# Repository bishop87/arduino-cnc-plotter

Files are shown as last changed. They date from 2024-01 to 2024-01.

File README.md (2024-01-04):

# CNC Plotter con Arduino

Progetto per realizzare un mini plotter cnc pilotato con arduino e motori passo passo 28byj-48

## Hardware

- 3 x motori passo passo 28byj-48 (io ho usato quelli a 5V)
- 3 x driver motori ULN2003 (solitamente venduti con i motori)
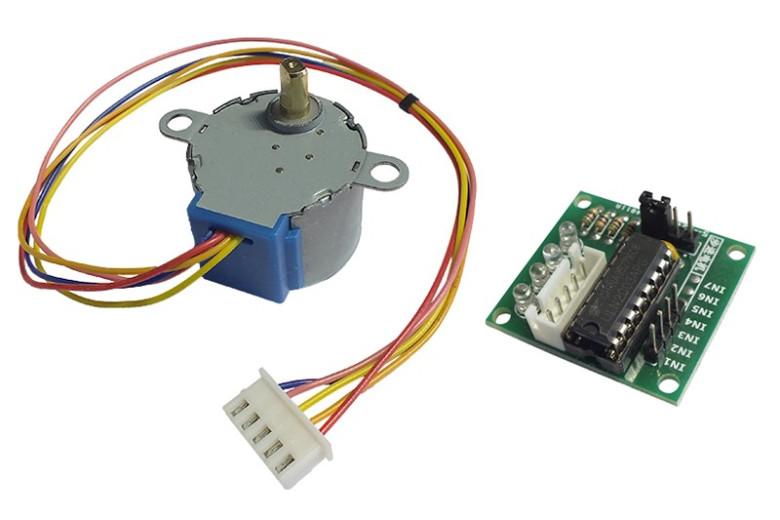
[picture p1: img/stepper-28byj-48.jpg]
stepper-28byj-48


- 1 x arduino nano
- 1 x cuscinetto a sfera tipo 608
- 1 x LM7805 (o modulo stepdown per ottenere 5V)
- 1 x alimentatore 12V
- Superficie di legno su cui fissare il materiale
- Viti varie di recupero
- Assi e supporti stampati in 3D, vedi sezione dedicata
- Pazienza, ne serve abbastanza

## Componenti 3D

Progetto Thingiverse principale da cui sono partito: https://www.thingiverse.com/thing:4796222 
Ho clonato i file stl per comodità e li ho messi nella cartella stl di questo repo:
- _SpurGear.stl_: ingranaggio da montare sul motore stepper (ne servono 2)
- _bearing_center.stl_: cilindro che restringe il foro del cuscinetto a sfera di tipo 608 per usarlo con una vite da 2-3mm di diametro
- _pen_cap.stl_: cappello da mettere sulla penna con un paio di elastici per rendere morbido l'appoggio della penna sul foglio
- _pen_holder.stl_: supporto che gestisce la penna e si fissa sul motore per l'asse Z, la parte centrale deve risultare mobile e alloggia una vite per bloccare la penna in posizione
- _plate_01.stl_: binario per l'asse Y
- _plate_02.stl_: asse Y con barra dentata
- _plate_03.stl_: binario per l'asse X
- _plate_04.stl_: asse X con barra dentata
- _prop.stl_: supporto da incollare al binario per l'asse X
- _prop_bearing_608.stl_: alternativa da usare al prop.stl se si ha un cuscinetto di tipo 608

## Assemblaggio

Video del progetto originale che illustra i vari passaggi principali sia di assemblaggio che della messa in funzione: https://www.youtube.com/watch?v=WtUIBxfddjw
Schema di collegamento dei 3 motori driver:
| Axis | Arduino |ULN2003|ULN2003|28BYJ-48|
|:---:|:---:|:-----:|:-----:|:---:|
| X-Axis | D5 |IN1 |OUT1 |BLUE |
| | D4 |IN2 |OUT2 |PINK |
| | D3 |IN3 |OUT3 |YELLOW  |
| | D2 |IN4 |OUT4 |ORANGE  |
| Y-Axis | A0 |IN1 |OUT1 |BLUE |
| | A1 |IN2 |OUT2 |PINK |
| | A2 |IN3 |OUT3 |YELLOW  |
| | A3 |IN4 |OUT4 |ORANGE  |
| Z-Axis | D13 |IN1 |OUT1 |BLUE |
| | D12 |IN2 |OUT2 |PINK |
| | D9 |IN3 |OUT3 |YELLOW  |
| | D8 |IN4 |OUT4 |ORANGE  |
| | | |+5V |RED |

## Software

 - **grbl Firmware per Arduino**: https://github.com/TGit-Tech/GRBL-28byj-48
Codice derivato dallo standard de facto per l'ambito cnc con Arduino **grbl**, consente di pilotare i 3 assi con i motori 28byj-48 ed i relativi driver più semplici dei normali stepper per cnc o stampanti 3d.
Copiare la cartella "grbl" che trovate per comodità anche in questo repo sotto il path ./lib-grbl nel path locale del PC con le librerie di ArduinoIDE (nel caso di macos /Users/nomeutente/Documents/Arduino/libraries/grbl).
 - **inkscape**: https://inkscape.org/
Famoso software open per manipolare e creare file vettoriali.
 - **jscut**: https://jscut.org/jscut.html
Consente di convertire file vettoriali svg contenenti path (eventuali font vanno convertiti in path prima con inkscape) in file gcode rispetto ai parametri della cnc configurati.
Nel path di questo repo (/jscut-settings/settings_20240105.jscut) c'è un esempio di impostazioni da caricare su jscut, nel caso è possible variare manualmente i settaggi, il pannello più importante si trova in masso a sinistra:
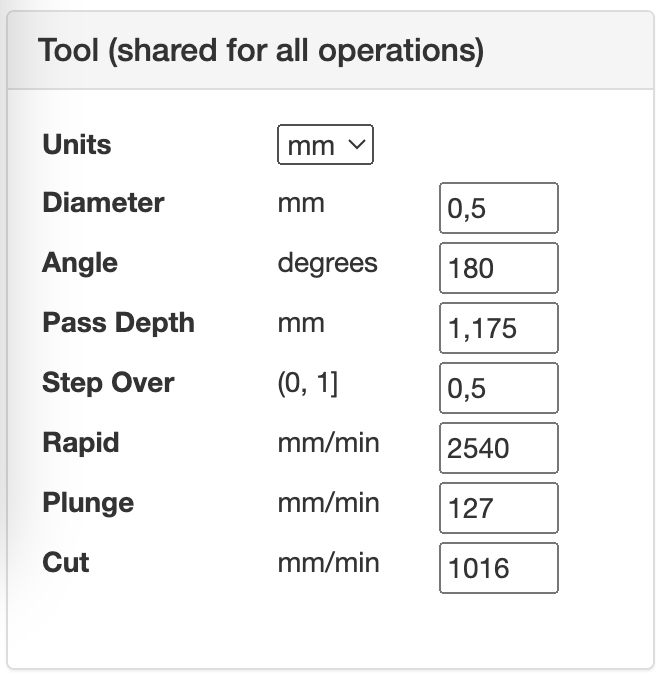
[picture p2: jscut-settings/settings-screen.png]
jscut-settings-screen


**Diameter** : sarebbe il diametro della fresa, nel nostro caso la larghezza del tratto disegnato dalla penna (più è fine più passate serviranno per disegnare)
**Pass Depth**: quanto dovrà andare in profondità la penna sull'asse z, si imposta un po' per tentativi
**Step Over**: percentuale di sovrapposizione delle varie passate, più il valore è basso più passate sovrapposte ci saranno, aumenterà di conseguenza il tempo e l'inchiostro usato.

- **UGS (Universal Gcode Sender)**: https://winder.github.io/ugs_website/
applicativo java based che consente di pilotare la cnc (il nostro arduino con firmware grbl) da PC via seriale (usb).
1. una volta aperto il programma selezionare la voce di menu "Machine" > "Setup Wizard"
2. Impostare i parametri di connessione alla porta seriale (firmware: GRBL; Port: nome della seriale a cui è collegato Arduino; baudrate: 115200), quindi cliccare "Connect"
3. Verificare la direzione degli assi X, Y, Z, ed eventualmente invertirla (io per la verità ho preferito invertire il connettore del driver su arduino per la X e la Y)
4. testare il movimento degli assi, misurando il reale spostamento rispetto al valore atteso ed inserire i parametri di step/mm calcolati dal programma (nel mio caso 72 step/mm sia per x che per y).
5. concludere il wizard senza modificare altro.

## Conclusioni

Alcune foto del risultato finale

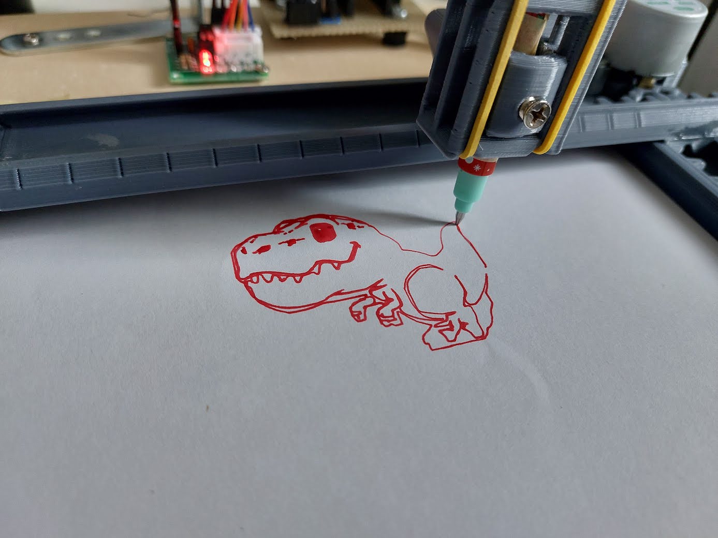
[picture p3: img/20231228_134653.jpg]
foto1


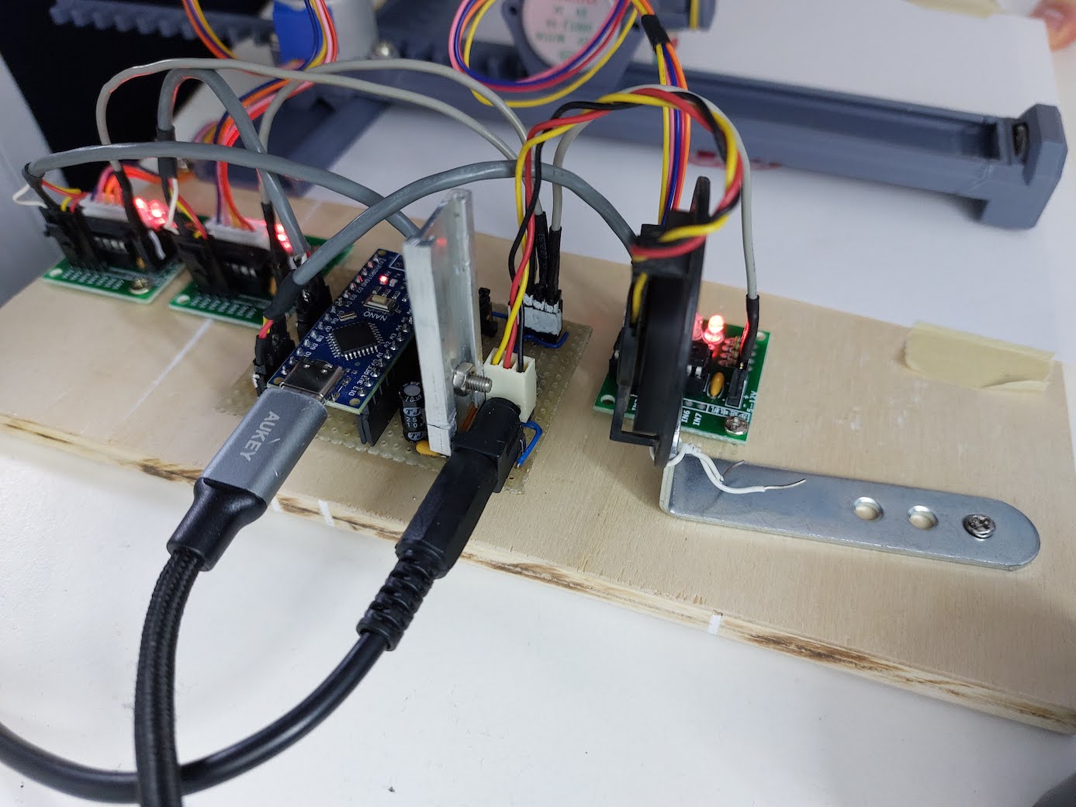
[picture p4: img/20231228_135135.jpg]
foto2


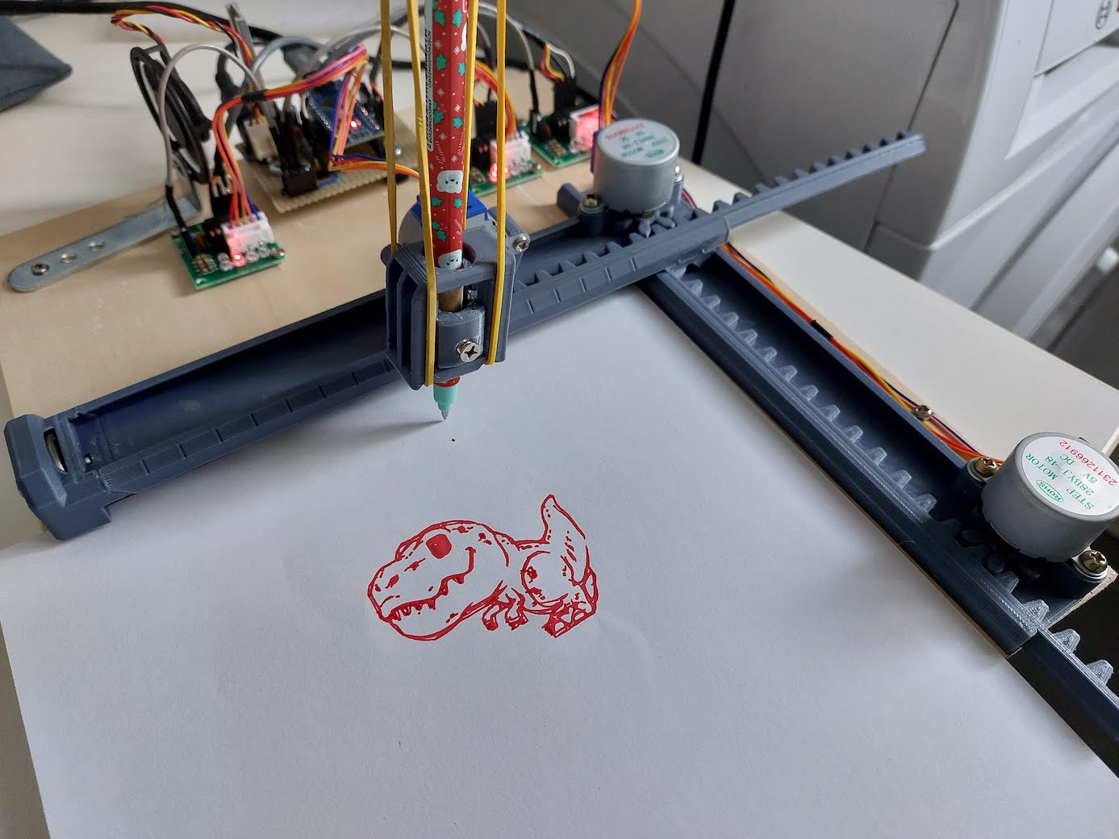
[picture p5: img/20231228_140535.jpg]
foto3


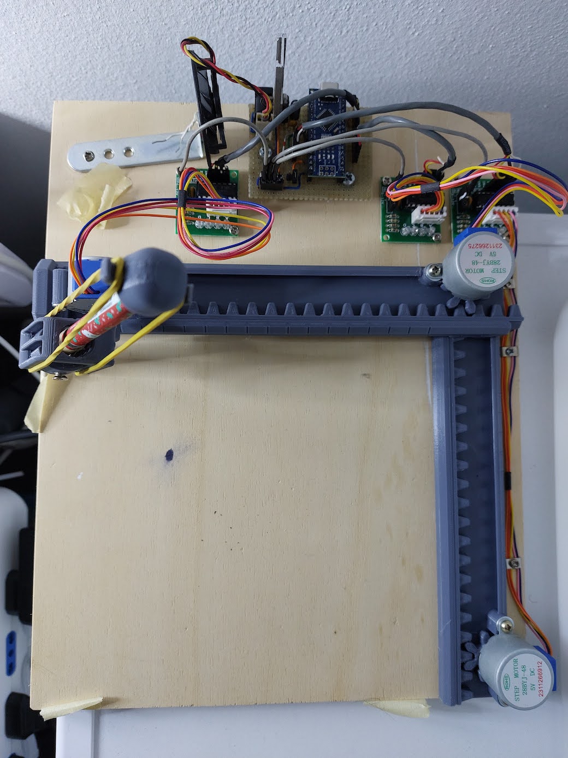
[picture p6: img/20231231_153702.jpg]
foto14


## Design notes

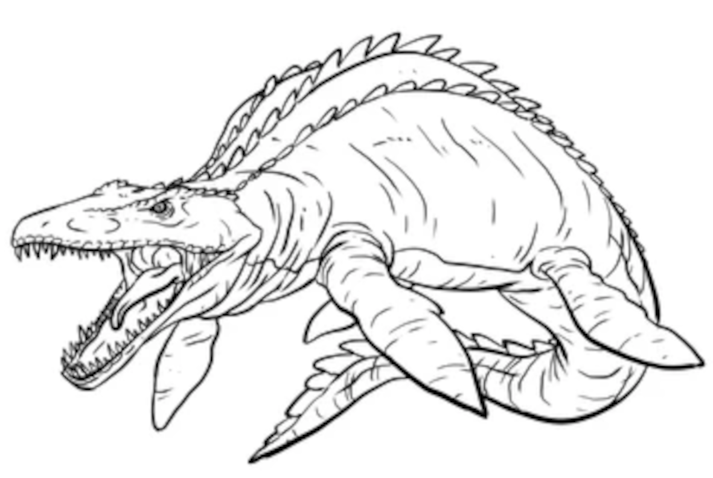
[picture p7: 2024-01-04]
example/mosa.png

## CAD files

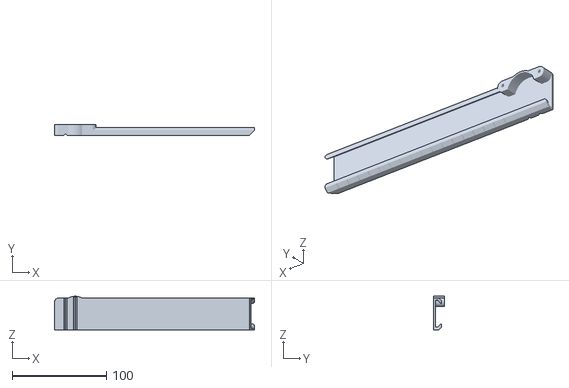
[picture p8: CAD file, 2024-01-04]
stl/plate_03.stl
211.7 x 11.5 x 35.6

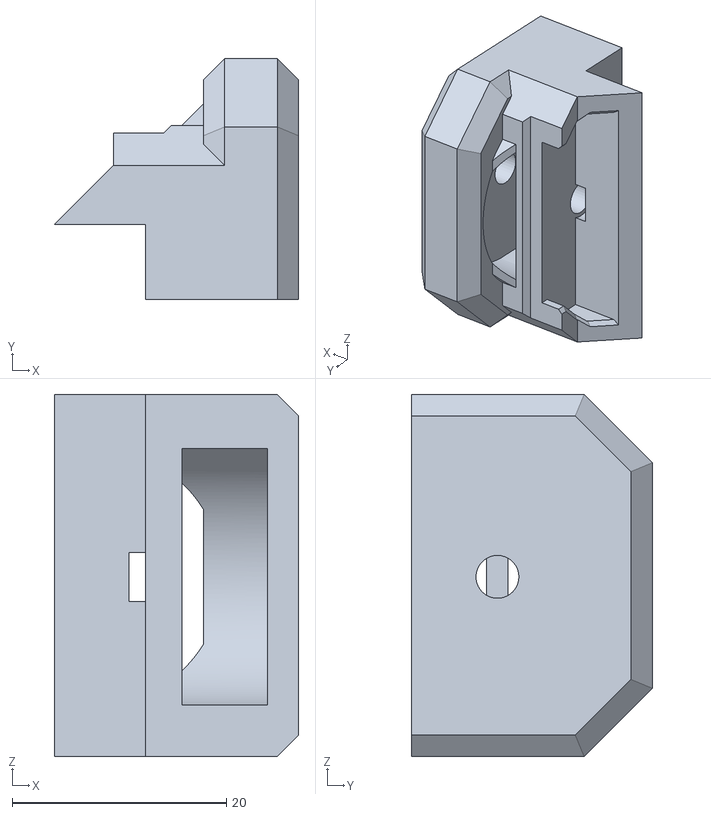
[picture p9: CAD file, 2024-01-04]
stl/prop_bearing_608.stl
22.8 x 22.4 x 33.8

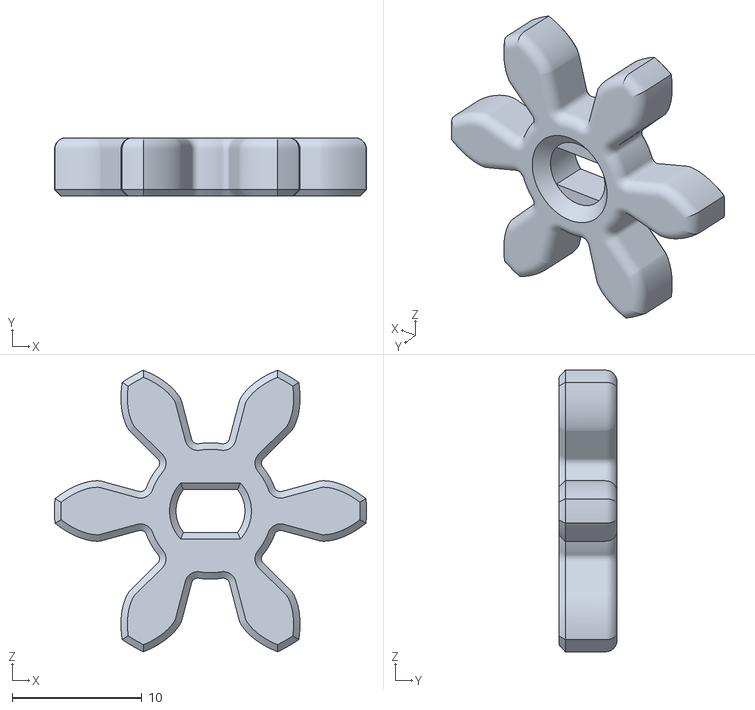
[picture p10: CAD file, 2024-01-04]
stl/SpurGear.stl
24.0 x 4.50 x 21.7

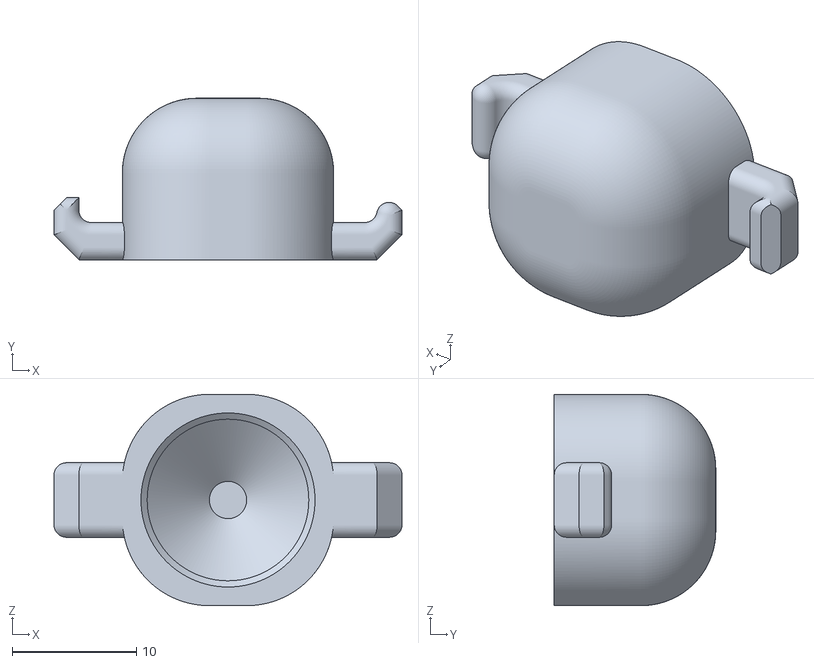
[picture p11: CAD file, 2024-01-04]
stl/pen_cap.stl
28.0 x 13.0 x 17.0

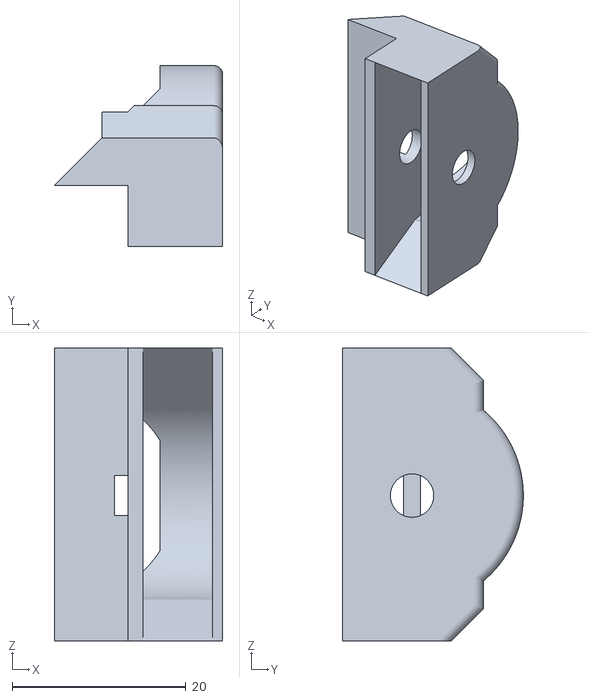
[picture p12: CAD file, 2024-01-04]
stl/prop.stl
19.4 x 20.8 x 33.8

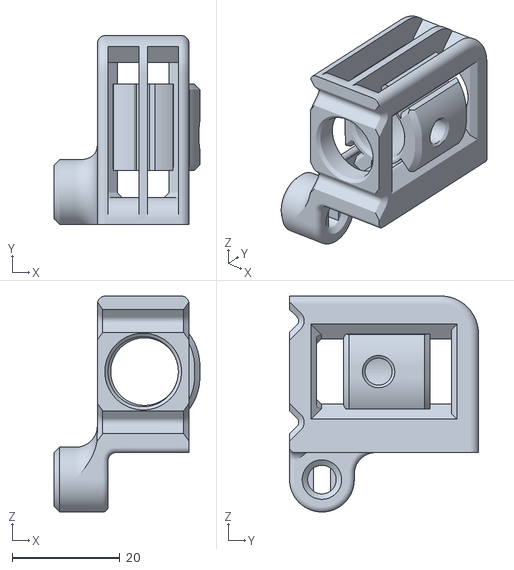
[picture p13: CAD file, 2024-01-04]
stl/pen_holder.stl
27.0 x 35.0 x 40.0

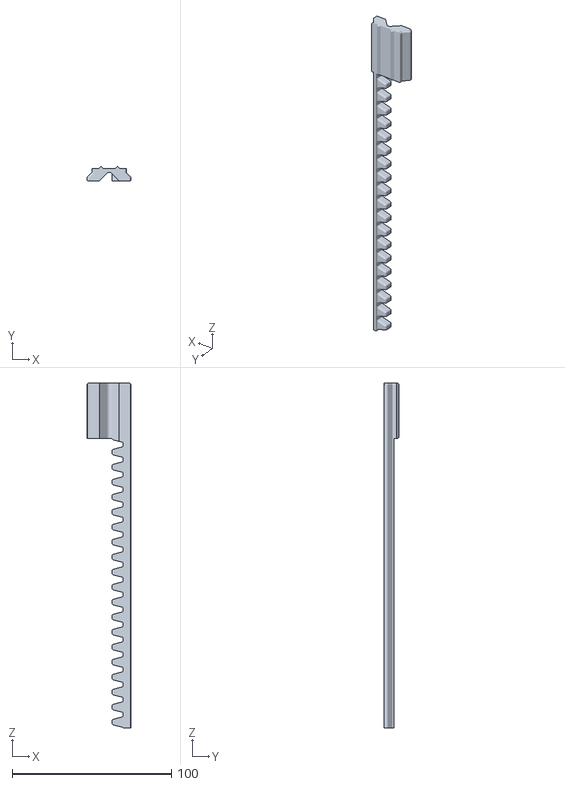
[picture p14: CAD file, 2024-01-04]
stl/plate_02.stl
27.9 x 9.16 x 216.8

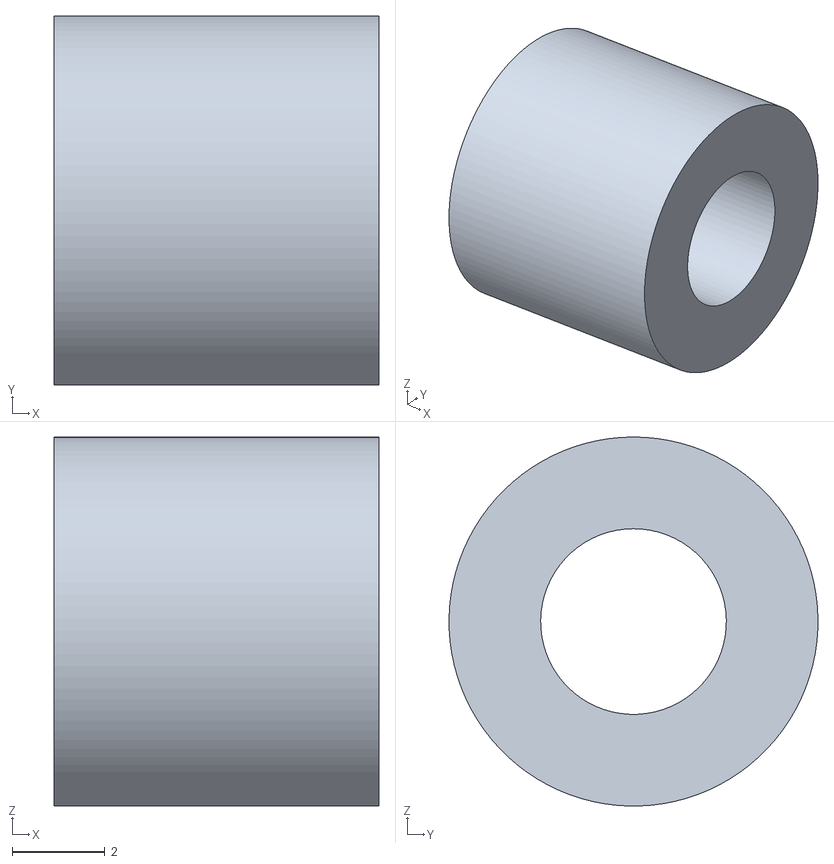
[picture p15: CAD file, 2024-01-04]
stl/bearing_center.stl
7.00 x 7.95 x 7.95

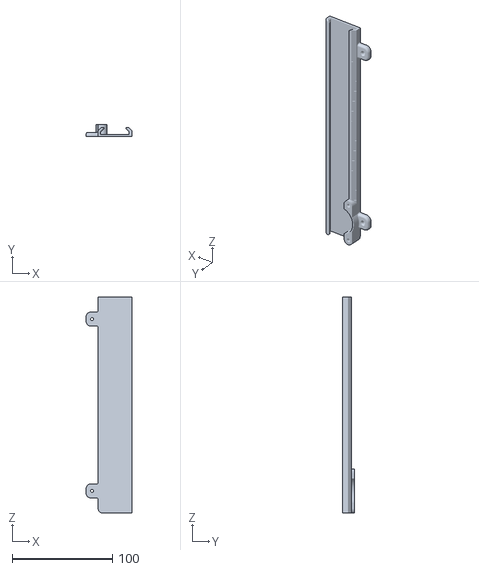
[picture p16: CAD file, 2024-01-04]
stl/plate_01.stl
45.8 x 11.5 x 215.2

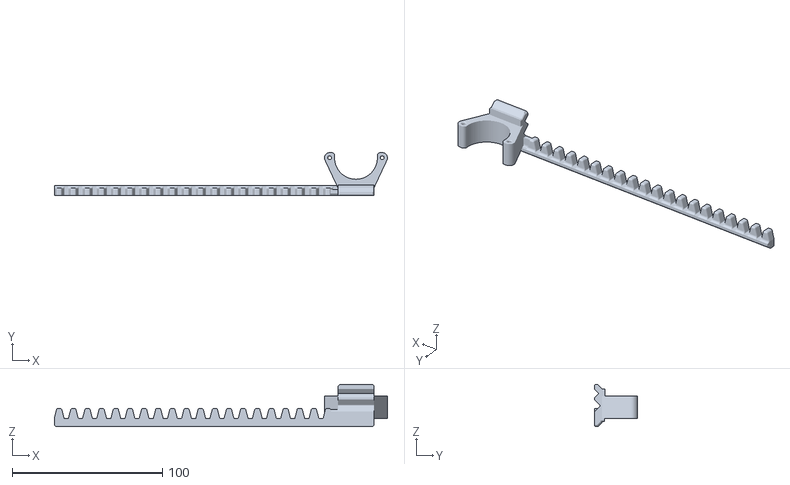
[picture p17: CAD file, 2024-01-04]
stl/plate_04.stl
221.8 x 28.5 x 28.0

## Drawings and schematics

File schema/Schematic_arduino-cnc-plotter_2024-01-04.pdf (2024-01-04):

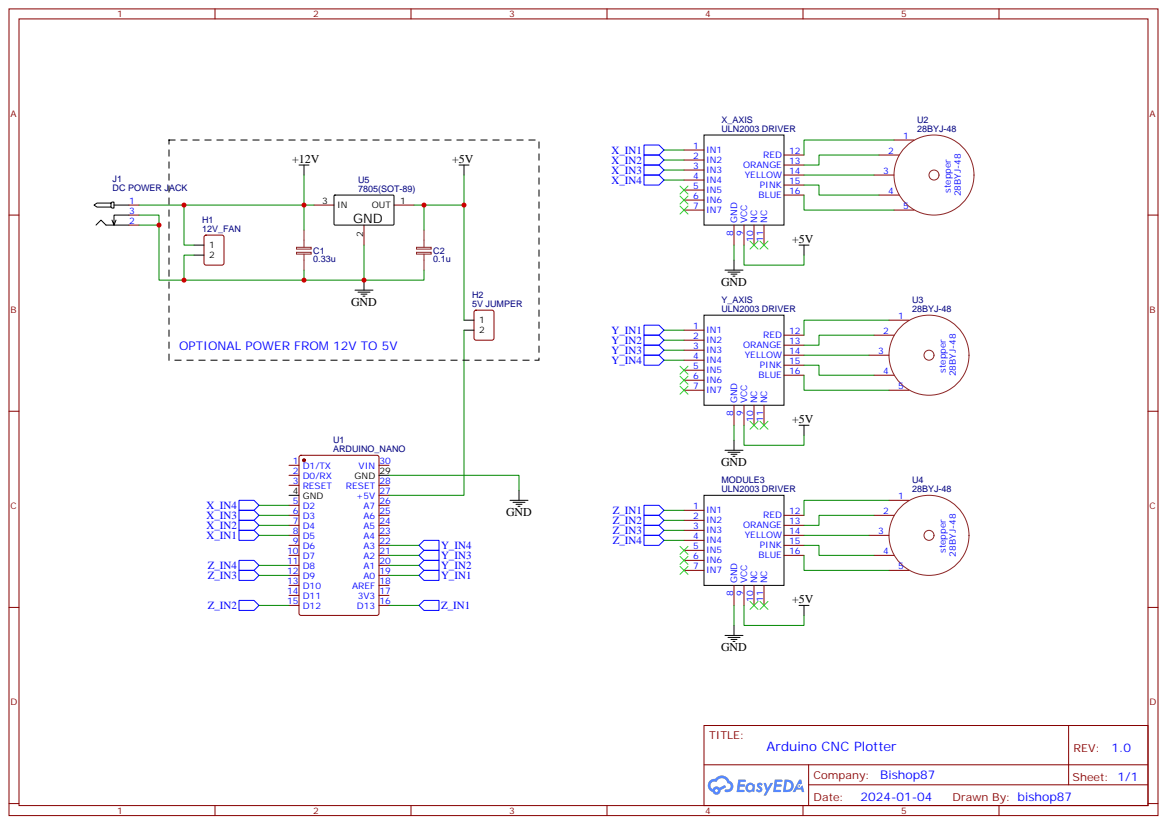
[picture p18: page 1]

PINK 15 YELLOW 14 ORANGE 13 RED 12

OPTIONAL POWER FROM 12V TO 5V

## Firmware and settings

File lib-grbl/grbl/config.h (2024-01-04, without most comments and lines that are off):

#define config_h
#include "grbl.h" // For Arduino IDE compatibility.
#define DEFAULTS_GENERIC
#define CPU_MAP_ATMEGA328P // Arduino Uno CPU
#define BAUD_RATE 115200
#define CMD_RESET 0x18 // ctrl-x.
#define CMD_STATUS_REPORT '?'
#define CMD_CYCLE_START '~'
#define CMD_FEED_HOLD '!'
#define CMD_SAFETY_DOOR 0x84
#define CMD_JOG_CANCEL  0x85
#define CMD_DEBUG_REPORT 0x86 // Only when DEBUG enabled, sends debug report in '{}' braces.
#define CMD_FEED_OVR_RESET 0x90         // Restores feed override value to 100%.
#define CMD_FEED_OVR_COARSE_PLUS 0x91
#define CMD_FEED_OVR_COARSE_MINUS 0x92
#define CMD_FEED_OVR_FINE_PLUS  0x93
#define CMD_FEED_OVR_FINE_MINUS  0x94
#define CMD_RAPID_OVR_RESET 0x95        // Restores rapid override value to 100%.
#define CMD_RAPID_OVR_MEDIUM 0x96
#define CMD_RAPID_OVR_LOW 0x97
#define CMD_SPINDLE_OVR_RESET 0x99      // Restores spindle override value to 100%.
#define CMD_SPINDLE_OVR_COARSE_PLUS 0x9A
#define CMD_SPINDLE_OVR_COARSE_MINUS 0x9B
#define CMD_SPINDLE_OVR_FINE_PLUS 0x9C
#define CMD_SPINDLE_OVR_FINE_MINUS 0x9D
#define CMD_SPINDLE_OVR_STOP 0x9E
#define CMD_COOLANT_FLOOD_OVR_TOGGLE 0xA0
#define CMD_COOLANT_MIST_OVR_TOGGLE 0xA1
#define HOMING_INIT_LOCK // Comment to disable
#define HOMING_CYCLE_0 (1<<Z_AXIS)                // REQUIRED: First move Z to clear workspace.
#define HOMING_CYCLE_1 ((1<<X_AXIS)|(1<<Y_AXIS))  // OPTIONAL: Then move X,Y at the same time.
#define N_HOMING_LOCATE_CYCLE 1 // Integer (1-128)
#define N_STARTUP_LINE 2 // Integer (1-2)
#define N_DECIMAL_COORDVALUE_INCH 4 // Coordinate or position value in inches
#define N_DECIMAL_COORDVALUE_MM   3 // Coordinate or position value in mm
#define N_DECIMAL_RATEVALUE_INCH  1 // Rate or velocity value in in/min
#define N_DECIMAL_RATEVALUE_MM    0 // Rate or velocity value in mm/min
#define N_DECIMAL_SETTINGVALUE    3 // Decimals for floating point setting values
#define N_DECIMAL_RPMVALUE        0 // RPM value in rotations per min.
#define MESSAGE_PROBE_COORDINATES // Enabled by default. Comment to disable.
#define SAFETY_DOOR_SPINDLE_DELAY 4.0 // Float (seconds)
#define SAFETY_DOOR_COOLANT_DELAY 1.0 // Float (seconds)
#define CHECK_LIMITS_AT_INIT
#define DEFAULT_FEED_OVERRIDE           100 // 100%. Don't change this value.
#define MAX_FEED_RATE_OVERRIDE          200 // Percent of programmed feed rate (100-255). Usually 120% or 200%
#define MIN_FEED_RATE_OVERRIDE           10 // Percent of programmed feed rate (1-100). Usually 50% or 1%
#define FEED_OVERRIDE_COARSE_INCREMENT   10 // (1-99). Usually 10%.
#define FEED_OVERRIDE_FINE_INCREMENT      1 // (1-99). Usually 1%.
#define DEFAULT_RAPID_OVERRIDE  100 // 100%. Don't change this value.
#define RAPID_OVERRIDE_MEDIUM    50 // Percent of rapid (1-99). Usually 50%.
#define RAPID_OVERRIDE_LOW       25 // Percent of rapid (1-99). Usually 25%.
#define DEFAULT_SPINDLE_SPEED_OVERRIDE    100 // 100%. Don't change this value.
#define MAX_SPINDLE_SPEED_OVERRIDE        200 // Percent of programmed spindle speed (100-255). Usually 200%.
#define MIN_SPINDLE_SPEED_OVERRIDE         10 // Percent of programmed spindle speed (1-100). Usually 10%.
#define SPINDLE_OVERRIDE_COARSE_INCREMENT  10 // (1-99). Usually 10%.
#define SPINDLE_OVERRIDE_FINE_INCREMENT     1 // (1-99). Usually 1%.
#define RESTORE_OVERRIDES_AFTER_PROGRAM_END // Default enabled. Comment to disable.
#define REPORT_FIELD_BUFFER_STATE // Default enabled. Comment to disable.
#define REPORT_FIELD_PIN_STATE // Default enabled. Comment to disable.
#define REPORT_FIELD_CURRENT_FEED_SPEED // Default enabled. Comment to disable.
#define REPORT_FIELD_WORK_COORD_OFFSET // Default enabled. Comment to disable.
#define REPORT_FIELD_OVERRIDES // Default enabled. Comment to disable.
#define REPORT_FIELD_LINE_NUMBERS // Default enabled. Comment to disable.
#define REPORT_OVR_REFRESH_BUSY_COUNT 20  // (1-255)
#define REPORT_OVR_REFRESH_IDLE_COUNT 10  // (1-255) Must be less than or equal to the busy count
#define REPORT_WCO_REFRESH_BUSY_COUNT 30  // (2-255)
#define REPORT_WCO_REFRESH_IDLE_COUNT 10  // (2-255) Must be less than or equal to the busy count
#define ACCELERATION_TICKS_PER_SECOND 100
#define ADAPTIVE_MULTI_AXIS_STEP_SMOOTHING  // Default enabled. Comment to disable.
#define TOOL_LENGTH_OFFSET_AXIS Z_AXIS // Default z-axis. Valid values are X_AXIS, Y_AXIS, or Z_AXIS.
#define MINIMUM_JUNCTION_SPEED 0.0 // (mm/min)
#define MINIMUM_FEED_RATE 1.0 // (mm/min)
#define N_ARC_CORRECTION 12 // Integer (1-255)
#define ARC_ANGULAR_TRAVEL_EPSILON 5E-7 // Float (radians)
#define DWELL_TIME_STEP 50 // Integer (1-255) (milliseconds)
#define ENABLE_RESTORE_EEPROM_WIPE_ALL         // '$RST=*' Default enabled. Comment to disable.
#define ENABLE_RESTORE_EEPROM_DEFAULT_SETTINGS // '$RST=$' Default enabled. Comment to disable.
#define ENABLE_RESTORE_EEPROM_CLEAR_PARAMETERS // '$RST=#' Default enabled. Comment to disable.
#define ENABLE_BUILD_INFO_WRITE_COMMAND // '$I=' Default enabled. Comment to disable.
#define FORCE_BUFFER_SYNC_DURING_EEPROM_WRITE // Default enabled. Comment to disable.
#define FORCE_BUFFER_SYNC_DURING_WCO_CHANGE // Default enabled. Comment to disable.
#define PARKING_AXIS Z_AXIS // Define which axis that performs the parking motion
#define PARKING_TARGET -5.0 // Parking axis target. In mm, as machine coordinate [-max_travel,0].
#define PARKING_RATE 500.0 // Parking fast rate after pull-out in mm/min.
#define PARKING_PULLOUT_RATE 100.0 // Pull-out/plunge slow feed rate in mm/min.
#define PARKING_PULLOUT_INCREMENT 5.0 // Spindle pull-out and plunge distance in mm. Incremental distance.
#define DISABLE_LASER_DURING_HOLD // Default enabled. Comment to disable.

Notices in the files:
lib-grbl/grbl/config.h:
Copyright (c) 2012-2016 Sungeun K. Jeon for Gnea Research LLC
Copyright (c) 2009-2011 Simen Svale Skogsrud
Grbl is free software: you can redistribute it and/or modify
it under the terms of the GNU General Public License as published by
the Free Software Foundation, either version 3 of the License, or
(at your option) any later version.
